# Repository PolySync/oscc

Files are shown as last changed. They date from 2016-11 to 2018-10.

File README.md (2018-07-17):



Open Source Car Control (OSCC) is an assemblage of software and hardware designs that enable computer control of modern cars in order to facilitate the development of autonomous vehicle technology. It is a modular and stable way of using software to interface with a vehicle’s communications network and control systems.

OSCC enables developers to send control commands to the vehicle, read control messages from the vehicle’s OBD-II CAN network, and forward reports for current vehicle control state. Such as steering angle & wheel speeds. Control commands are issued to the vehicle component ECUs via the steering wheel torque sensor, throttle position sensor, and brake position sensor. (Because the gas-powered Kia Soul isn’t brake by-wire capable, an auxiliary actuator is added to enable braking.) This low-level interface means that OSCC offers full-range control of the vehicle without altering the factory safety-case, spoofing CAN messages, or hacking ADAS features.

Although OSCC currently supports only the 2014 or later Kia Soul (petrol and EV), the API and firmware have been designed to make it easy to add new vehicle support. Additionally, the separation between API and firmware means it is easier to modify and test parts of your program without having to update the flashed OSCC modules.

Our [Wiki](https://github.com/PolySync/OSCC/wiki) is in the process of being updated to reflect the new changes, but contains a bunch of valuable information to help you get started in understanding the details of the system.

**DriveKit:** If you're looking for a turn-key solution, we offer a commercially-supported vehicle control interface called DriveKit. DriveKit is a complete system for by-wire control of Kia Soul EV and Kia Niro Hybrid vehicles. It includes an integrated control module, automotive-grade wiring harnesses, e-stop switch, and additional vehicle control features –– plus it installs in under an hour. **Visit https://polysync.io/drivekit/ for more information.**

# Versions

New versions of the API and the firmware are released periodically as new features are added and bugs are
fixed. **It is of vital importance that you update whenever there is a new version so that you can be certain
you are not using a version with known safety issues.**

There are four versions to be aware of:

* **Sensor Interface Board (throttle and steering):** the version is printed on the front of the shield

* **Vehicle Control Module (EV brakes):** the version is printed on the front of the shield

* **Actuator Control Board (petrol brakes):** the version is printed on the front of the shield

* **API and Firmware:** a single version is shared by both and listed in the [Releases section](https://github.com/PolySync/oscc/releases) of the repository.

The following table can be used to ensure that you use the appropriate firmware version with your boards:

| | Board Version | Firmware Version |
| --- | --- | --- |
| Sensor Interface | >= 1.0.0 | >= 1.0.0 |
| Vehicle Control | 0.1.0 | >= 1.1.0 |
| Actuator Control | >= 1.2.0 | >= 1.0.0 |
| | < 1.2.0 __*__ | >= 1.0.1 |

__*__ *Later versions of the Actuator Control Board utilize new pins to perform additional safety checks on startup. To use the new firmware on older boards, please see additional instructions in the [build](#brake-startup-test) section.*

# Repository Contents

* **api** - Software API, so your program can seamlessly talk to our modules.
* **firmware** - Arduino libraries and firmware for the OSCC modules.
* **hardware** - PCB schematics and board designs for control modules.

# Boards

The sensor interface and actuator control board schematics and design files are located in the
`hardware/boards` directory.

Thanks to [Trey German](https://www.polymorphiclabs.com) for
help designing the boards.

# Building and Uploading Firmware

The OSCC Project is built around a number of individual firmware modules that inter-operate to allow communication with your vehicle.
These modules are built from Arduinos and Arduino shields designed specifically for interfacing with various vehicle components.
Once these modules have been installed in the vehicle and flashed with the firmware, the API can be used to
receive reports from the car and send spoofed commands.

## Pre-requisites

You must have Arduino Core (version 1.8.5 or greater) and CMake (version 2.8 or greater) installed on
your machine.

```
sudo apt install build-essential cmake
```

A manual Arduino install is required since the debian package is older than 1.8.5
```
sudo apt-get purge arduino arduino-core
wget http://arduino.cc/download.php?f=/arduino-1.8.5-linux64.tar.xz -O arduino-1.8.5.tar.xz
tar -xf arduino-1.8.5.tar.xz
cd arduino-1.8.5
sudo mkdir -p /usr/share/arduino
sudo cp -R * /usr/share/arduino
```

OSCC uses CMake to avoid some of the limitations of the Arduino IDE. Using this method you can build
and upload the firmware from the command-line.

Check out [Arduino CMake](https://github.com/arduino-cmake/arduino-cmake) for more information.

## Building the Firmware

Navigate to the `firmware` directory and create a build directory inside of it:

```
cd firmware
mkdir build
cd build
```

To generate Makefiles, tell `cmake` which vehicle to build for by supplying the
appropriate build flag:

| Vehicle | Flag |
| --- | --- |
| Kia Soul Petrol | -DVEHICLE=kia_soul |
| Kia Soul EV | -DVEHICLE=kia_soul_ev |
| Kia Niro | -DVEHICLE=kia_niro |

For example, if you want to build firmware for the petrol Kia Soul:

```
cmake .. -DVEHICLE=kia_soul
```

**Operator Overrides: While all OSCC modules have operator override detection enabled by default, attempting to grab the steering wheel while the system is active could result in serious injury. The preferred method of operator override for steering is to utilize the brake pedal or E-stop button. To disable operator override for the steering module, pass an additional flag to the CMake build step.**

```
cmake .. -DVEHICLE=kia_soul -DSTEERING_OVERRIDE=OFF
```

If steering operator overrides remain enabled, the sensitivity can be adjusted by changing the value of the `TORQUE_DIFFERENCE_OVERRIDE_THRESHOLD` in the corresponding vehicle's header file.

* Lowering this value will make the steering module more sensitive to operator override, but will result in false positives around high-torque areas, such as the mechanical limits of the steering rack or when quickly and rapidly changing direction.
* Increasing this value will result in fewer false positives, but will make it more difficult to manually override the wheel.

By default, your firmware will have debug symbols which is good for debugging but increases
the size of the firmware significantly. To compile without debug symbols and optimizations
enabled, use the following instead:

```
cmake .. -DVEHICLE=kia_soul -DCMAKE_BUILD_TYPE=Release
```

**NOTE:**
> For older (< 1.2.0) versions of the actuator control board, you need to set an additional flag using `cmake .. -DKIA_SOUL=ON -DBRAKE_STARTUP_TEST=OFF` to disable startup tests that are not compatible with the previous board design.

This will generate the necessary files for building.

Now you can build all of the firmware with `make`:

```
make
```

If you'd like to build only a specific module, you can provide a target name to
`make` for whichever module you'd like to build:

```
make brake
make can-gateway
make steering
make throttle
```

## Uploading the Firmware

Once the firmware is successfully built, you can upload it. When you connect to
an Arduino with a USB cable, your machine assigns a serial device to it with the
path `/dev/ttyACM#` where `#` is a digit starting at 0 and increasing by one with
each additional Arduino connected.

You can upload firmware to a single module or to all modules. By default, `cmake`
is configured to expect each module to be `/dev/ttyACM0`, so if you connect a
single module to your machine, you can flash it without changing anything:

```
make throttle-upload
```

However, if you want to flash all modules, you need to change the ports in
`cmake` for each module to match what they are on your machine. The easiest way
is to connect each module in alphabetical order (brake, CAN gateway, steering,
throttle) so that they are assigned `/dev/ttyACM0` through `/dev/ttyACM3` in
a known order. You can then change the ports during the `cmake ..` step:

```
cmake .. -DVEHICLE=kia_soul -DSERIAL_PORT_BRAKE=/dev/ttyACM0 -DSERIAL_PORT_CAN_GATEWAY=/dev/ttyACM1 -DSERIAL_PORT_STEERING=/dev/ttyACM2 -DSERIAL_PORT_THROTTLE=/dev/ttyACM3
```

Then you can flash all with one command:

```
make all-upload
```

Sometimes it takes a little while for the Arduino to initialize once connected, so if there is an
error thrown initially, wait a little bit and then retry the command.

## Monitoring Arduino Modules

It is sometimes useful to monitor individual Arduino modules to check for proper operation and to
debug. If the modules have been built with the flag `-DCMAKE_BUILD_TYPE=Debug`, their debug
printing functionality will be enabled and they will print status information to the serial interface.

The GNU utility `screen` is one option to communicate with the Arduino via serial over USB. It can
be used to both receive the output of any `Serial.print` statements in your Arduino code, and to
push commands over serial to the Arduino. If you don't already have it installed,
you can get it with the following command:

```
sudo apt install screen
```

You need to enable debug mode with `-DDEBUG=ON` and tell `cmake` what serial port
the module you want to monitor is connected to
(see [section on uploading](#uploading-the-firmware) for details on the default
ports for each module). The default baud rate is `115200` but you can change it:

```
cmake .. -DVEHICLE=kia_soul -DDEBUG=ON -DSERIAL_PORT_THROTTLE=/dev/ttyACM0 -DSERIAL_BAUD_THROTTLE=19200
```

You can use a module's `monitor` target to automatically run `screen`, or a
module's `monitor-log` target to run `screen` and output to a file called
`screenlog.0` in the module's build directory:

```
make brake-monitor
make brake-monitor-log
```

You can exit `screen` with `C-a \`.

To do more in-depth debugging you can use any of a number of serial monitoring applications.
Processing can be used quite effectively to provide output plots of data incoming across a serial
connection.

Be aware that using serial printing can affect the timing of the firmware. You may experience
strange behavior while printing that does not occur otherwise.

# Controlling Your Vehicle - an Example Application

Now that all your Arduino modules are properly setup, it is time to start sending control commands.

We've created an example application, joystick commander, that uses the OSCC API to interface with the firmware, allowing you to send commands using a game controller and receive reports from the on-board OBD-II CAN. These commands are converted into CAN messages, which the OSCC API sends to the respective Arduino modules and are used to actuate the vehicle.

[OSCC Joystick Commander](https://github.com/PolySync/oscc-joystick-commander)

We've also created a ROS node, that uses the OSCC API to interface with the firmware from ROS messages, allowing you to send commands and receive reports in ROS.

[ROSCCO](https://github.com/PolySync/roscco)

# OSCC API

**Open and close CAN channel to OSCC Control CAN.**

```c
oscc_result_t oscc_open( uint channel );
oscc_result_t oscc_close( uint channel );
```

These methods are the start and end points of using the OSCC API in your application. ```oscc_open``` will open a socket connection
on the specified CAN channel, enabling it to quickly receive reports from and send commands to the firmware modules.
When you are ready to terminate your application, ```oscc_close``` can terminate the connection.

**NOTE:**
> The OSCC API catches the SIGIO signal which is asserted when a CAN frame is received on the CAN socket, and sets up a SIGIO signal handler
> to forward valid CAN messages to your application. If you have a section of code that is susceptible to conflicts with interrupts,
> you should temporarily block the SIGIO signal for the duration of that section and unblock it afterward.

**Enable and disable all OSCC modules.**

```c
oscc_result_t oscc_enable( void );
oscc_result_t oscc_disable( void );
```

After you have initialized your CAN connection to the firmware modules, these methods can be used to enable or disable the system. This
allows your application to choose when to enable sending commands to the firmware. Although you can only send commands when the system is
enabled, you can receive reports at any time.

**Publish control command to the corresponding module.**

```c
oscc_result_t publish_brake_position( double normalized_position );
oscc_result_t publish_steering_torque( double normalized_torque );
oscc_result_t publish_throttle_position( double normalized_position );
```

These commands will forward a double value to the specified firmware module. The double values are [0.0, 1.0] for brake and throttle,
and [-1.0, 1.0] for steering where -1.0 is counterclockwise and 1.0 is clockwise. The API will construct the appropriate values to send
as spoofed voltages to the vehicle to achieve the desired state. The API also contains safety checks to ensure no voltages outside of
the vehicle's expected range are sent.

**NOTE:**
> Each of these functions must be called at least once every 200ms to prevent the modules from detecting a loss of communication to the
> controlling computer (at which point they would disable themselves).

**Register callback function to handle OSCC report and OBD messages.**

```c
oscc_result_t subscribe_to_brake_reports( void(*callback)(oscc_brake_report_s *report) );
oscc_result_t subscribe_to_steering_reports( void(*callback)(oscc_steering_report_s *report) );
oscc_result_t subscribe_to_throttle_reports( void(*callback)(oscc_throttle_report_s *report) );
oscc_result_t subscribe_to_fault_reports( void(*callback)(oscc_fault_report_s *report) );
oscc_result_t subscribe_to_obd_messages( void(*callback)(struct can_frame *frame) );
```

In order to receive reports from the modules, your application will need to register a callback handler with the OSCC API.
When the appropriate report for your callback function is received from the API's socket connection, it will then forward the
report to your software.

Each module's reports are described in their respective wiki sections:

* [Brake (EV)](https://github.com/PolySync/oscc/wiki/Firmware-Brake-%28EV%29#brake-report)
* [Brake (Petrol)](https://github.com/PolySync/oscc/wiki/Firmware-Brake-%28Petrol%29#brake-report)
* [Steering](https://github.com/PolySync/oscc/wiki/Firmware-Steering#steering-report)
* [Throttle](https://github.com/PolySync/oscc/wiki/Firmware-Throttle#throttle-report)

In addition to OSCC specific reports, it will also forward any non-OSCC reports to any callback function registered with
```subscribe_to_obd_messages```. This can be used to view CAN frames received from the vehicle's OBD-II CAN channel. If you know
the corresponding CAN frame's id, you can parse reports sent from the car.

# Tests

There are two types of tests available: unit and property-based.

## Test Dependencies

The unit tests and property-based tests each have their own set of dependencies
required to run the tests.

For the unit tests you must have **Cucumber 2.0.0** and its dependency **Boost** installed:

```
sudo apt install ruby-dev libboost-dev
sudo gem install cucumber -v 2.0.0
```

For the property-based tests you must have **Rust**, its build manager **Cargo**, and **libclang**:

```
sudo apt install rustc cargo clang libclang-dev
```

## Running Tests

Building and running the tests is similar to the firmware itself, but you must instead tell
`cmake` to build the tests instead of the firmware with the `-DTESTS=ON` flag. We also pass
the `-DCMAKE_BUILD_TYPE=Release` flag so that `cmake` will disable debug symbols and enable
optimizations, good things to do when running tests to ensure nothing breaks with
optimizations. Lastly, you must tell the tests which vehicle header to use for
the tests (e.g., `-DVEHICLE=kia_soul`).

```
cd firmware
mkdir build
cd build
cmake .. -DTESTS=ON -DCMAKE_BUILD_TYPE=Release -DVEHICLE=kia_soul
```

### Unit Tests

Each module has a suite of unit tests that use **Cucumber** with **Cgreen**. There are pre-built
64-bit Linux versions in `firmware/common/testing/framework`.

Boost is required for Cucumber-CPP and has been statically linked into `libcucumber-cpp.a`.
If you need to build your own versions you can use the provided script `build_test_framework.sh`
which will install the Boost dependencies (needed for building), clone the needed
repositories with specific hashes, build the Cgreen and Cucumber-CPP libraries,
and place static Boost in the Cucumber-CPP library.

The built libraries will be placed in an `oscc_test_framework` directory in the
directory that you ran the script from. You can then copy `oscc_test_framework/cucumber-cpp`
and `oscc_test_framework/cgreen` to `firmware/common/testing/framework`.

We can run all of the unit tests available:

```
make run-unit-tests
```

Each module's test can also be run individually:

```
make run-brake-unit-tests
make run-can-gateway-unit-tests
make run-steering-unit-tests
make run-throttle-unit-tests
```

If everything works correctly you should see something like this:

```
# language: en
Feature: Receiving commands

  Commands received from a controller should be processed and acted upon.

  Scenario Outline: Enable throttle command sent from controller        # firmware/throttle/tests/features/receiving_commands.feature:8
    Given throttle control is disabled                                  # firmware/throttle/tests/features/receiving_commands.feature:9
    And the accelerator position sensors have a reading of <sensor_val> # firmware/throttle/tests/features/receiving_commands.feature:10
    When an enable throttle command is received                         # firmware/throttle/tests/features/receiving_commands.feature:12
    Then control should be enabled                                      # firmware/throttle/tests/features/receiving_commands.feature:14
    And the last command timestamp should be set                        # firmware/throttle/tests/features/receiving_commands.feature:15
    And <dac_a_val> should be written to DAC A                          # firmware/throttle/tests/features/receiving_commands.feature:16
    And <dac_b_val> should be written to DAC B                          # firmware/throttle/tests/features/receiving_commands.feature:17

    Examples:
      | sensor_val | dac_a_val | dac_b_val |
      | 0          | 0         | 0         |
      | 256        | 1024      | 1024      |
      | 512        | 2048      | 2048      |
      | 1024       | 4096      | 4096      |
```

### Property-Based Tests

The throttle, steering, and brake modules, along with the PID controller library, also contain a series of
property-based tests.

We can run all of the property-based tests available:

```
make run-property-tests
```

Each module's test can also be run individually:

```
make run-brake-property-tests
make run-steering-property-tests
make run-throttle-property-tests
make run-pid-library-property-tests
```

Once the tests have completed, the output should look similar to the following:

```
running 7 tests
test check_integral_term ... ok
test check_derivative_term ... ok
test check_proportional_term ... ok
test check_reversed_inputs ... ok
test check_same_control_for_same_inputs ... ok
test check_zeroize ... ok

test result: ok. 7 passed; 0 failed; 0 ignored; 0 measured

   Doc-tests tests

running 0 tests

test result: ok. 0 passed; 0 failed; 0 ignored; 0 measured
```

### All Tests

Finally, as a convenience you can run all available tests:

```
make run-all-tests
```

# Additional Vehicles & Contributing

OSCC currently has information regarding the Kia Soul PS (2014-2018), but we want to grow! The
repository is structured to facilitate including more vehicles as more is learned about them.

In order to include information related to a new vehicle's specification, follow the format defined in ```api/include/vehicles/kia_soul.h``` and
add a `cmake` option to choose your new header when compiling the API.

Please see [CONTRIBUTING.md](CONTRIBUTING.md).

# License Information

Hardware source materials (e.g. schematics, board layouts, wiring diagrams, data sheets, physical
installation documentation, 3D models, etc.) for the OSCC (Open Source Car Control) Project are
licensed under Creative Commons Attribution-ShareAlike 4.0 International (CC BY-SA 4.0).

Firmware  and software source for the OSCC (Open Source Car Control) Project is licensed under the
MIT License (MIT) unless otherwise noted (e.g. 3rd party dependencies, etc.).

Please see [LICENSE.md](LICENSE.md) for more details.

# Contact Information

Please direct questions regarding OSCC and/or licensing to help@polysync.io.

*Distributed as-is; no warranty is given.*

Copyright (c) 2017 PolySync Technologies, Inc.  All Rights Reserved.

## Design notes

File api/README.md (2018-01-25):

# Getting started with the OSCC API

There are a few options on how to get started with your own application that
uses the OSCC API.

## The library approach

To build both `libosccapi.so` and `libosccapi.a` for the Kia Soul EV,
you can run the following commands on Linux from this directory.
```
mkdir build && cd build
cmake -DKIA_SOUL_EV=ON ..
make
```
Substitute `-DKIA_SOUL_EV` for another supported vehicle if the EV isn't your
target. For example `-DKIA_SOUL=ON` will build the libraries with support
for the Kia Soul Petrol instead.

### Using `libosccapi.so`
Using the shared library for a project that uses the OSCC API is easy!
The following is an example `CMakeLists.txt` for doing just that. This example
is all you need for a project with it's own source file, `main.c`.
```
cmake_minimum_required(VERSION 2.8)
project(an_example)
set(OSCC_API_INSTALL /path_to/oscc_directory/api)
link_directories(${OSCC_API_INSTALL}/build)
set(OSCC_INCLUDES ${OSCC_API_INSTALL}/include)
set(SOURCES ${CMAKE_SOURCE_DIR}/src/main.c)
add_executable(${PROJECT_NAME} ${SOURCES})
target_include_directories(${PROJECT_NAME} PUBLIC ${OSCC_INCLUDES})
target_link_libraries(${PROJECT_NAME} PUBLIC osccapi)
```

### Using `libosccapi.a`
Using the static library isn't much different than the shared one,
the CMakeLists.txt just requires the full path to the library as it doesn't
intuit it from a provided link_directory.
```
cmake_minimum_required(VERSION 2.8)
project(an_example)
set(OSCC_API_INSTALL /path_to/oscc_directory/api)
set(OSCC_INCLUDES ${OSCC_API_INSTALL}/include)
set(SOURCES ${CMAKE_SOURCE_DIR}/src/main.c)
add_executable(${PROJECT_NAME} ${SOURCES})
target_include_directories(${PROJECT_NAME} PUBLIC ${OSCC_INCLUDES})
target_link_libraries(${PROJECT_NAME} PUBLIC ${OSCC_API_INSTALL}/build/libosccapi.a)
```

## Straight from the sources
Another approach is to just include the OSCC API source code in your project.
Since the OSCC API has no dependencies beyond a Linux system, this is easy too!
Here's an example CMakeLists.txt that takes the straight from the sources
approach. Note that it makes the assumption that we're building for the Kia
Soul Petrol with the `"-DKIA_SOUL=ON"`.

```
cmake_minimum_required(VERSION 2.8)
project(an_example)
set(OSCC_API_INSTALL /path_to/oscc_directory/api)
set(OSCC_INCLUDES ${OSCC_API_INSTALL}/include ${OSCC_API_INSTALL}/src)
set(SOURCES ${CMAKE_SOURCE_DIR}/src/main.c ${OSCC_API_INSTALL}/src/oscc.c)
add_executable(${PROJECT_NAME} ${SOURCES})
target_compile_definitions(${PROJECT_NAME} PUBLIC "-DKIA_SOUL=ON")
target_include_directories(${PROJECT_NAME} PUBLIC ${OSCC_INCLUDES})
```

## Using the API

Let's walk through actually writing some code that uses the OSCC API, an example
program that listens to all the information that OSCC reports. Feel free to
experiment with this code, if it's all put into a `main.c` you can use
any of the CMakeLists.txt options above to build it.

First, we'll do some generic setup. This isn't a requriement of the OSCC API
but might make our example a little more useful.

```
#include <stdio.h> // printf
#include <signal.h> // SIGINT
#include <unistd.h> // usleep
```
Okay, now for the actual OSCC API include that allows us to initiate,
listen to each message type and then properly release OSCC. `oscc.h` is
all you need!

```
#include "oscc.h" // oscc_open, oscc_disable, oscc_close and each subscribe.
```
In order for our example to trigger the proper cleanup when we press `Ctrl+C`
to quit the program, we'll setup a signal handler to let us know.

```
// Global indication of Ctrl+C.
static int EXIT_SIGNALED = OSCC_OK;

// Help exiting gracefully.
void signal_handler(int signal_number)
{
    if (signal_number == SIGINT)
    {
        EXIT_SIGNALED = OSCC_ERROR;
    }
}
```

Now lets walk through our OSCC message subscribers. When we get a report from
something OSCC provides, let's print a message reporting what we see.

__Throttle__
```
void throttle_callback(oscc_throttle_report_s * report)
{
    printf("Hello from throttle_callback!\n");
}
```
__Steering__
```
void steering_callback(oscc_steering_report_s * report)
{
    printf("steering_callback reporting!\n");
}
```
__Brake__
```
void brake_callback(oscc_brake_report_s * report)
{
    printf("'Brake-ing' news from the brake_callback!\n");
}
```
__Fault__
```
void fault_callback(oscc_fault_report_s * report)
{
    printf("Oh! Something caused a fault and we made it to the fault_callback. We're seeing a ");

    if (report->fault_origin_id == FAULT_ORIGIN_BRAKE)
    {
        printf("brake fault!\n");
    }
    else if (report->fault_origin_id == FAULT_ORIGIN_STEERING)
    {
        printf("steering fault!\n");
    }
    else if (report->fault_origin_id == FAULT_ORIGIN_THROTTLE)
    {
        printf("throttle fault!\n");
    }
}
```
__OBD__
```
static void obd_callback(struct can_frame * frame)
{
    printf("From the obd_callback, CAN ID: %x\n", frame->can_id);
}
```
Okay, we're all setup! Let get to work! Our code base is pretty small so
we'll just stick to the `main` function
```
int main
{
```
Now let's put that 'Ctrl+C' setup we did earlier to use.
```
    struct sigaction sig;
    sig.sa_handler = signal_handler;
    sigaction(SIGINT, &sig, NULL);
```
Next we need to tell OSCC where to to send it's messages.
```
    oscc_subscribe_to_obd_messages(obd_callback);
    oscc_subscribe_to_brake_reports(brake_callback);
    oscc_subscribe_to_steering_reports(steering_callback);
    oscc_subscribe_to_throttle_reports(throttle_callback);
    oscc_subscribe_to_fault_reports(fault_callback);
```
In order to verify that initalizing OSCC succeeds and clean things up
if we fail, we need a way to capture results.
```
    oscc_result_t return_value;
```
For brevity, we'll assume that we're opening CAN channel 0 to connect to OSCC
and spin it up!
```
    int channel = 0;
    return_value = oscc_open(channel);
```
Since we captured the result of out call to oscc_open, we can verify it
succeded before moving on or signal that we need to clean things up.
```
    if(return_value != OSCC_OK)
    {
        printf("Error in oscc_open!\n");
        EXIT_SIGNALED = OSCC_ERROR;
    }
```

Now we wait, just let the callbacks to their work. To avoid loading the
CPU with this example, we'll sleep for a bit (50ms) on each iteration.
```
    while(EXIT_SIGNALED == OSCC_OK)
    {
        (void) usleep(50000);
    }
```

Once we're through, we can clean things up.
```
    oscc_disable();
    oscc_close(channel);
```

Don't forget to close up the `main` function!
```
}
```

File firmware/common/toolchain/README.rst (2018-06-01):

=============
Arduino CMake
=============


Arduino is a great development platform, which is easy to use. It has everything a beginner should need. The *Arduino IDE* simplifies a lot of things for the standard user, but if you are a professional programmer the IDE can feel simplistic and restrictive.

One major drawback of the *Arduino IDE* is that you cannot do anything without it, which for me is a **complete buzz kill**. Thats why queezythegreat created an alternative build system for the Arduino using CMake. With the original repository not being updated since 2014 and lacking some important features like support for the latest Arduino SDKs, we decided to fix things up for 1.6; now that some people have started using this as their preferred fork, we decided to accept our fate of being the current maintainers.

CMake is great cross-platform build system that works on practically any operating system. With it you are not constrained to a single build system. CMake lets you generate the build system that fits your needs, using the tools you like. It can generate any type of build system, from simple Makefiles, to complete projects for Eclipse, Visual Studio, XCode, etc.

The **Arduino CMake** build system integrates tightly with the *Arduino SDK*.

*Arduino SDK* version **0.19** or higher is required.

So if you like to do things from the command line (using make), or to build your firmware where you're in control, or if you would like to use an IDE such as Eclipse, KDevelop, XCode, CodeBlocks or something similar,  then **Arduino CMake** is the system for you.

Features
--------

* Integrates with *Arduino SDK*
* Supports all Arduino boards.
* Supports Arduino type libraries.
* Automatic detection of Arduino libraries.
* Generates firmware images.
* Generates built-in examples.
* Generates libraries.
* Sketch support.
* Upload support.
* Hardware Platform support.
* Programmer support (with bootloader upload).
* Supports multiple build system types (Makefiles, Eclipse, KDevelop, CodeBlocks, XCode, etc).
* Cross-platform: Windows, Linux, Mac.
* Extensible build system, thanks to CMake.

Feedback
--------

**Arduino CMake** is hosted on GitHub and is available on multiple forks (At the time of writing up to **161(!)**),
with one the more advanced and maintainable being the following:

https://github.com/arduino-cmake/arduino-cmake/

However, none of this would have been possible with the generous bunch of work the original author queezythegreat invested into this project, who definately earns most of the credit for getting things running:

https://github.com/queezythegreat/arduino-cmake

We want to stress again that he did all the initial work to even make CMake spit out Arduino firmwares. Without the effort queezythegreat put into this, we would not have been able to even think about getting an Arduino 1.6 project running. This is by no means a hostile fork and we would give him ownership of the organization as well at any time, should he wish so.

Did you find a bug or would like a specific feature, please report it at:

https://github.com/arduino-cmake/arduino-cmake/issues

If you would like to hack on this project, don't hesitate to fork it on GitHub.
We will be glad to integrate your changes if you send me a ``Pull Request``.

Requirements
------------

* Base requirements:

  - ``CMake`` - http://www.cmake.org/cmake/resources/software.html
  - ``Arduino SDK`` - http://www.arduino.cc/en/Main/Software

* Linux requirements:

  - ``gcc-avr``      - AVR GNU GCC compiler
  - ``binutils-avr`` - AVR binary tools
  - ``avr-libc``     - AVR C library
  - ``avrdude``      - Firmware uploader

Contributors
------------

I would like to thank the following people for contributing to **Arduino CMake**:

* Juan José Herrero Barbosa (`Souler`_)
* Bei Chen Liu (`Baycken`_)
* MrPointer (`MrPointer`_)
* Marc Plano-Lesay (`Kernald`_)
* James Goppert (`jgoppert`_)
* Matt Tyler (`matt-tyler`_)
* Andrew Stromme (`astromme`_)
* `johnyb`_
* `arunh`_
* Sebastian Herp (`sebastianherp`_)
* Michael Daffin (`james147`_)
* Pavel Ilin (`PIlin`_)
* Igor Mikolic-Torreira (`igormiktor`_)
* Claudio Henrique Fortes Felix (`chffelix`_)
* Alexandre Tuleu (`atuleu`_)
* `getSurreal`_
* Sebastian Zaffarano (`szaffarano`_)
* `cheshirekow`_
* Logan Engstrom (`meadowstream`_) 
* Francisco Ramírez (`franramirez688`_)
* Brendan Shillingford (`bshillingford`_)
* Mike Purvis (`mikepurvis`_) 
* Steffen Hanikel (`hanikesn`_)
* Tomasz Bogdal (`queezythegreat`_) (original author of arduino-cmake)
* Jonas (`JonasProgrammer`_)

.. _Souler: https://github.com/Souler
.. _Baycken: https://github.com/Baycken
.. _MrPointer: https://github.com/MrPointer
.. _Kernald: https://github.com/Kernald
.. _jgoppert: https://github.com/jgoppert
.. _matt-tyler: https://github.com/matt-tyler
.. _astromme: https://github.com/astromme
.. _johnyb: https://github.com/johnyb
.. _arunh: https://github.com/arunh
.. _sebastianherp: https://github.com/sebastianherp
.. _james147: https://github.com/james147
.. _PIlin: https://github.com/PIlin
.. _igormiktor: https://github.com/igormiktor
.. _chffelix: https://github.com/chffelix
.. _atuleu: https://github.com/atuleu
.. _getSurreal: https://github.com/getSurreal
.. _szaffarano: https://github.com/szaffarano
.. _cheshirekow: https://github.com/cheshirekow
.. _meadowstream: https://github.com/meadowstream
.. _franramirez688: https://github.com/franramirez688
.. _bshillingford: https://github.com/bshillingford
.. _mikepurvis: https://github.com/mikepurvis
.. _hanikesn: https://github.com/hanikesn
.. _queezythegreat: https://github.com/queezythegreat
.. _JonasProgrammer: https://github.com/JonasProgrammer

License
-------
This Source Code Form is subject to the terms of the Mozilla Public
License, v. 2.0. If a copy of the MPL was not distributed with this file,
You can obtain one at http://mozilla.org/MPL/2.0/.

TODO
----

* Test more complex configurations and error handling

Contents
--------

1. `Getting Started`_
2. `Using Arduino CMake`_

   1. `Creating Firmware Images`_
   2. `Creating Libraries`_
   3. `Arduino Sketches`_
   4. `Arduino Built-in Examples`_
   5. `Arduino Libraries`_
   6. `Arduino Library Examples`_
   7. `Compiler and Linker Flags`_
   8. `Programmers`_
   9. `Pure AVR Development`_
   10. `Advanced Options`_
   11. `Miscellaneous Functions`_
   12. `Bundling Arduino CMake`_

3. `Linux Environment`_

   1. `Linux Serial Naming`_
   2. `Linux Serial Terminals`_

4. `Mac OS X Environment`_

   1. `Mac Serial Naming`_
   2. `Mac Serial Terminals`_

5. `Windows Environment`_

   1. `CMake Generators`_
   2. `Windows Serial Naming`_
   3. `Windows Serial Terminals`_

6. `Eclipse Environment`_
7. `Troubleshooting`_

   1. `undefined reference to `__cxa_pure_virtual'`_
   2. `Arduino Mega 2560 image does not work`_
   3. `Library not detected automatically`_
   4. `error: attempt to use poisoned "SIG_USART0_RECV"`_

8. `Resources`_

Getting Started
---------------

The following instructions are for **\*nix** type systems, specifically this is a Linux example.

In short you can get up and running using the following commands::

    mkdir build
    cd build
    cmake ..
    make
    make upload              # to upload all firmware images             [optional]
    make blink-serial  # to get a serial terminal to wire_serial   [optional]

For a more detailed explanation, please read on...

1. Toolchain file
   
   In order to build firmware for the Arduino you have to specify a toolchain file to enable cross-compilation. There are two ways of specifying the file, either at the command line or from within the *CMakeLists.txt* configuration files. The bundled example uses the second approach like so::

        set(CMAKE_TOOLCHAIN_FILE ${CMAKE_SOURCE_DIR}/cmake/ArduinoToolchain.cmake)

   Please note that this must be before the ``project(...)`` command.
   
   If you would like to specify it from the command line, heres how::

        cmake -DCMAKE_TOOLCHAIN_FILE=../path/to/toolchain/file.cmake PATH_TO_SOURCE_DIR

2. Creating a build directory

   The second order of business is creating a build directory. CMake has a great feature called out-of-source builds, what this means is the building is done in a completely separate directory from where the sources are. The benefit of this is you don't have any clutter in you source directory and you won't accidentally commit something that is auto-generated.

   So let's create that build directory::

        mkdir build
        cd build

3. Creating the build system

   Now let's create the build system that will create our firmware::

        cmake ..

   To specify the build system type, use the ``-G`` option, for example::

        cmake -G"Eclipse CDT4 - Unix Makefiles" ..

   If you rather use a GUI, use::

        cmake-gui ..

4. Building

   Next we will build everything::

        make

5. Uploading

   Once everything built correctly we can upload. Depending on your Arduino you will have to update the serial port used for uploading the firmware. To change the port please edit the following variable in *CMakeLists.txt*::

        set(${FIRMWARE_NAME}_PORT /path/to/device)

   Ok lets do a upload of all firmware images::

        make upload

   If you have an upload sync error then try resetting/ power cycling the board before starting the upload process.

6. Serial output

   If you have some serial output, you can launch a serial terminal from the build system. The command used for executing the serial terminal is user configurable by the following setting::

        set(${FIRMWARE_NAME}_SERIAL serial command goes here)

   In order to get access to the serial port use the following in your command::

        @SERIAL_PORT@

   That constant will get replaced with the actual serial port used (see uploading). In the case of our example configuration we can get the serial terminal by executing the following::

        make blink-serial

Using Arduino CMake
-------------------

In order to use **Arduino CMake** just include the toolchain file, everything will get set up for building. You can set the toolchain
in `CMakeList.txt` like so::

        set(CMAKE_TOOLCHAIN_FILE ${CMAKE_SOURCE_DIR}/cmake/ArduinoToolchain.cmake)

Please note that this must be before the ``project(...)`` command.

You can also specify it at build configuration time::

        cmake -DCMAKE_TOOLCHAIN_FILE=../path/to/toolchain/file.cmake PATH_TO_SOURCE_DIR

Creating Firmware Images
~~~~~~~~~~~~~~~~~~~~~~~~

Once you have the **Arduino CMake** loaded you can start defining firmware images.

To create Arduino firmware in CMake you use the ``generate_arduino_firmware`` command. The full syntax of the command is::

    generate_arduino_firmware(target_name
         [BOARD board_name]
         [BOARD_CPU board_cpu]
         [SKETCH sketch_path | SRCS  src1 src2 ... srcN]
         [HDRS  hdr1 hdr2 ... hdrN]
         [LIBS  lib1 lib2 ... libN]
         [PORT  port]
         [SERIAL serial_cmd]
         [PROGRAMMER programmer_id]
         [AFLAGS flags]
         [NO_AUTOLIBS])

The options are:

+--------------------+----------------------------------------------------------------------+----------------------------------------+
| **Name**           | **Description**                                                      | **REQUIRED**                           |
+--------------------+----------------------------------------------------------------------+----------------------------------------+
| **BOARD**          | Board name *(such as uno, mega2560, ...)*                            | **REQUIRED**                           |
+--------------------+----------------------------------------------------------------------+----------------------------------------+
| **BOARD_CPU**      | Board CPU *(such as atmega328, atmega168, ...)*                      | **REQUIRED** if board cpu is ambiguous |
+--------------------+----------------------------------------------------------------------+----------------------------------------+
| **SKETCH**         | Sketch path (see `Arduino Sketches`_)                                | **SKETCH or SRCS are REQUIRED**        |
+--------------------+----------------------------------------------------------------------+----------------------------------------+
| **SRCS**           | Source files                                                         | **SKETCH or SRCS are REQUIRED**        |
+--------------------+----------------------------------------------------------------------+----------------------------------------+
| **HDRS**           | Headers files *(for project based build systems)*                    |                                        |
+--------------------+----------------------------------------------------------------------+----------------------------------------+
| **LIBS**           | Libraries to link (see `Creating libraries`_)                        |                                        |
+--------------------+----------------------------------------------------------------------+----------------------------------------+
| **PORT**           | Serial port, for upload and serial targets (see `Upload Firmware`_)  |                                        |
+--------------------+----------------------------------------------------------------------+----------------------------------------+
| **SERIAL**         | Serial command for serial target (see `Serial Terminal`_)            |                                        |
+--------------------+----------------------------------------------------------------------+----------------------------------------+
| **PROGRAMMER**     | Programmer ID, enables programmer burning (see `Programmers`_).      |                                        |
+--------------------+----------------------------------------------------------------------+----------------------------------------+
| **ARDLIBS**        | Manual list of Arduino type libraries, common use case is when the   |                                        |
|                    | library header name does not match the librarie's directory name.    |                                        |
|                    | **ADVANCED OPTION!** Can be used in conjuction with **NO_AUTOLIBS**. |                                        |
+--------------------+----------------------------------------------------------------------+----------------------------------------+
| **AFLAGS**         | avrdude flags for target                                             |                                        |
+--------------------+----------------------------------------------------------------------+----------------------------------------+
| **NO_AUTOLIBS**    | Disable Arduino library detection *(default On)*                     |                                        |
+--------------------+----------------------------------------------------------------------+----------------------------------------+
| **MANUAL**         | Disable Arduino Core (enables pure AVR development)                  |                                        |
+--------------------+----------------------------------------------------------------------+----------------------------------------+

You can specify the options in two ways, either as the command arguments or as variables. When specifying the options as variables they must be named::

    ${TARGET_NAME}_${OPTION_NAME}

Where **${TARGET_NAME}** is the name of you target and **${OPTION_NAME}** is the name of the option.

So to create a target (firmware image) called ``blink``, composed of ``blink.h`` and ``blink.cpp`` source files for the *Arduino Uno*, you write the following::

    set(blink_SRCS  blink.cpp)
    set(blink_HDRS  blink.h)
    set(blink_BOARD uno)

    generate_arduino_firmware(blink)

The previous example can be rewritten as::

    generate_arduino_firmware(blink
          SRCS  blink.cpp
          HDRS  blink.h
          BOARD uno)

Upload Firmware
_______________

To enable firmware upload functionality, you need to add the ``PORT`` option::

    set(blink_SRCS  blink.cpp)
    set(blink_HDRS  blink.h)
    set(blink_PORT /dev/ttyUSB0)
    set(blink_BOARD nano)
    set(blink_BOARD_CPU atmega328) # required because nano has atmega328 and atmega168 models

    generate_arduino_firmware(blink)

Or::

    generate_arduino_firmware(blink
          SRCS  blink.cpp
          HDRS  blink.h
          PORT  /dev/ttyUSB0
          BOARD_CPU atmega328
          BOARD nano)

Once defined there will be two targets available for uploading, ``${TARGET_NAME}-upload`` and a global ``upload`` target (which will depend on all other upload targets defined in the build):

* ``blink-upload`` - will upload just the ``blink`` firmware
* ``upload`` - upload all firmware images registered for uploading

Serial Terminal
_______________
To enable serial terminal, use the ``SERIAL`` option (``@SERIAL_PORT@`` will be replaced with the ``PORT`` option)::

    set(blink_SRCS  blink.cpp)
    set(blink_HDRS  blink.h)
    set(blink_PORT  /dev/ttyUSB0)
    set(blink_SERIAL picocom @SERIAL_PORT@ -b 9600 -l)
    set(blink_BOARD uno)

    generate_arduino_firmware(blink)

Alternatively::

    generate_arduino_firmware(blink
          SRCS  blink.cpp
          HDRS  blink.h
          PORT  /dev/ttyUSB0
          SERIAL picocom @SERIAL_PORT@ -b 9600 -l
          BOARD uno)

This will create a target named ``${TARGET_NAME}-serial`` (in this example: blink-serial).

Creating Libraries
~~~~~~~~~~~~~~~~~~

Creating libraries is very similar to defining a firmware image, except we use the ``generate_arduino_library`` command. This command creates static libraries, and are not to be confused with `Arduino Libraries`_. The full command syntax::

    generate_arduino_library(name
         [BOARD board_name]
         [BOARD_CPU board_cpu]
         [SRCS  src1 src2 ... srcN]
         [HDRS  hdr1 hdr2 ... hdrN]
         [LIBS  lib1 lib2 ... libN]
         [NO_AUTOLIBS])

The options are:

+--------------------+------------------------------------------------------+----------------------------------------+
| **Name**           | **Description**                                      | **REQUIRED**                           |
+--------------------+------------------------------------------------------+----------------------------------------+
| **BOARD**          | Board name *(such as uno, mega2560, ...)*            | **REQUIRED**                           |
+--------------------+------------------------------------------------------+----------------------------------------+
| **BOARD_CPU**      | Board CPU *(such as atmega328, atmega168, ...)*      | **REQUIRED** if board cpu is ambiguous |
+--------------------+------------------------------------------------------+----------------------------------------+
| **SRCS**           | Source files                                         | **REQUIRED**                           |
+--------------------+------------------------------------------------------+----------------------------------------+
| **HDRS**           | Headers files *(for project based build systems)*    |                                        |
+--------------------+------------------------------------------------------+----------------------------------------+
| **LIBS**           | Libraries to link *(sets up dependency tracking)*    |                                        |
+--------------------+------------------------------------------------------+----------------------------------------+
| **NO_AUTOLIBS**    | Disable Arduino library detection *(default On)*     |                                        |
+--------------------+------------------------------------------------------+----------------------------------------+
| **MANUAL**         | Disable Arduino Core (enables pure AVR development)  |                                        |
+--------------------+------------------------------------------------------+----------------------------------------+

You can specify the options in two ways, either as the command arguments or as variables. When specifying the options as variables they must be named::

    ${TARGET_NAME}_${OPTION_NAME}

Where **${TARGET_NAME}** is the name of you target and **${OPTION_NAME}** is the name of the option.

Let's define a simple library called ``blink_lib`` with two sources files for the *Arduino Uno*::

    set(blink_lib_SRCS  blink_lib.cpp)
    set(blink_lib_HDRS  blink_lib.h)
    set(blink_lib_BOARD uno)

    generate_arduino_library(blink_lib)

The other way of defining the same thing is::

    generate_arduino_library(blink_lib
        SRCS  blink_lib.cpp
        HDRS  blink_lib.h
        BOARD uno)

Once that library is defined we can use it in our other firmware images... Let's add ``blink_lib`` to the ``blink`` firmware::

    set(blink_SRCS  blink.cpp)
    set(blink_HDRS  blink.h)
    set(blink_LIBS  blink_lib)
    set(blink_BOARD uno)

    generate_arduino_firmware(blink)

CMake has automatic dependency tracking, so when you build the ``blink`` target, ``blink_lib`` will automatically get built, in the right order.

Arduino Sketches
~~~~~~~~~~~~~~~~

To build a Arduino sketch use the **SKETCH** option (see `Creating firmware images`_). For example::

    set(blink_SKETCH  ${ARDUINO_SDK_PATH}/examples/1.Basics/Blink) # Path to sketch directory
    set(blink_BOARD   uno)

    generate_arduino_firmware(blink)

This will build the **blink** example from the **Arduino SDK**.

Note: When specifying the sketch directory path, arduino-cmake is expecting to find a sketch file named after the directory (with a extension of .pde or .ino).

You can also specify the path to the main sketch file, then the parent directory of that sketch will be search for additional sketch files.

Arduino Built-in Examples
~~~~~~~~~~~~~~~~~~~~~~~~~

The Arduino SDK comes with a handful of code examples, providing an easy setup for simple operations.
Since there are many examples, they were categorized, making each example be under a certain category.
Each example consists of at least one source file, named after the example and has the *.ino* or *.pde* extension, and sits under a directory which is also named after the example.
Each category is a directory named after it, having all its examples as sub-directories, named after them.
One such example is ``Blink``, probrably the most popular one as well. It's located under the ``Basics`` category and has a source file named ``Blink.ino``.

**Arduino CMake** has the abillity to automatically generate these examples, simply by passing their name and optionally their category, as some sort of an optimization. **It supports case-insensitive names**
If you would like to generate and upload some of those examples you can use the `generate_arduino_example` command. The syntax of the command is::

    generate_arduino_example(target_name
                             [EXAMPLE example_name]
                             [BOARD board_name]
                             [BOARD_CPU board_cpu]
                             [CATEGORY category_name]
                             [PORT port]
                             [SERIAL serial command]
                             [PORGRAMMER programmer_id]
                             [AFLAGS avrdude_flags])

The options are:

+--------------------+----------------------------------------------------------------------+----------------------------------------+
| **Name**           | **Description**                                                      | **REQUIRED**                           |
+--------------------+----------------------------------------------------------------------+----------------------------------------+
| **EXAMPLE**        | Example name.                                                        | **REQUIRED**                           |
+--------------------+----------------------------------------------------------------------+----------------------------------------+
| **BOARD**          | Board name *(such as uno, mega2560, ...)*                            | **REQUIRED**                           |
+--------------------+----------------------------------------------------------------------+----------------------------------------+
| **BOARD_CPU**      | Board CPU *(such as atmega328, atmega168, ...)*                      | **REQUIRED** if board cpu is ambiguous |
+--------------------+----------------------------------------------------------------------+----------------------------------------+
| **CATEGORY**       | Category name.                                                       |                                        |
+--------------------+----------------------------------------------------------------------+----------------------------------------+
| **PORT**           | Serial port, for upload and serial targets (see `Upload Firmware`_)  |                                        |
+--------------------+----------------------------------------------------------------------+----------------------------------------+
| **SERIAL**         | Serial command for serial target (see `Serial Terminal`_)            |                                        |
+--------------------+----------------------------------------------------------------------+----------------------------------------+
| **PROGRAMMER**     | Programmer ID, enables programmer burning (see `Programmers`_).      |                                        |
+--------------------+----------------------------------------------------------------------+----------------------------------------+
| **AFLAGS**         | avrdude flags for target                                             |                                        |
+--------------------+----------------------------------------------------------------------+----------------------------------------+

To generate a target for the **blink** example from the **Basics** category for the **Uno** board::

    generate_arduino_example(blink_example
                             CATEGORY Basics
                             EXAMPLE Blink
                             BOARD uno
                             PORT  /dev/ttyUSB0)

You can also rewrite the previous like so::

    set(blink_example_CATEGORY Basics)
    set(blink_example_EXAMPLE Blink)
    set(blink_example_BOARD uno)
    set(blink_example_PORT /dev/ttyUSB0)

    generate_arduino_example(blink_example)

The previous example will generate the following two target::

    blink_example
    blink_example-upload
    
**Note:** The above example will work perfectly fine even if the ``Basics`` category hadn't been passed.

Arduino Libraries
~~~~~~~~~~~~~~~~~

Libraries are one of the more powerful features which the Arduino offers to users. Instead of rewriting code, people bundle their code in libraries and share them with others.
The structure of these libraries is very simple, which makes them easy to create.

An Arduino library is **any directory which contains a header named after the directory**, simple.
Any source files contained within that directory are part of the library. Here is a example of library a called ExampleLib::

    ExampleLib/
      |-- ExampleLib.h
      |-- ExampleLib.cpp
      `-- OtherLibSource.cpp

Now because the power of Arduino lies within those user-created libraries, support for them is built right into **Arduino CMake**. The **Arduino SDK** comes with a large number of default libraries and adding new libraries is simple.

To incorporate a library into your firmware, you can do one of three things:

1. Place the library next to the default Arduino libraries (located at **${ARDUINO_SDK}/libraries**)
2. Place the library next to the firmware configuration file (same directory as the **CMakeLists.txt**)
3. Place the library in a separate folder and tell **Arduino CMake** the path to that directory.
   
   To tell CMake where to search for libraries use the `link_directories` command. The command has to be used before defining any firmware or libraries requiring those libraries.
   
   For example::
     
      link_directories(${CMAKE_CURRENT_SOURCE_DIR}/libraries)
      link_directories(/home/username/arduino_libraries)

If a library contains nested sources, a special option must be defined to enable recursion. For example to enable recursion for the Arduino Wire library use::

    set(Wire_RECURSE True)

The option name should be **${LIBRARY_NAME}_RECURSE**, where in this case **LIBRARY_NAME** is equal to *Wire*.

Arduino Libraries are not to be confused with normal static libraries (for exmaple *system libraries* or libraries created using generate_arduino_library). The **LIBS** option only accepts static libraries, so do not list the Arduino Libraries in that option (as you will get an error).

Arduino Library Examples
~~~~~~~~~~~~~~~~~~~~~~~~

Most Arduino libraries have examples bundled with them. If you would like to generate and upload some of those examples you can use the `generate_arduino_library_example` command. The syntax of the command is::

    generate_arduino_library_example(target_name
                             [LIBRARY library_name]
                             [EXAMPLE example_name]
                             [BOARD  board_name]
                             [BOARD_CPU board_cpu]
                             [PORT port]
                             [SERIAL serial command]
                             [PORGRAMMER programmer_id]
                             [AFLAGS avrdude_flags])

The options are:

+--------------------+----------------------------------------------------------------------+----------------------------------------+
| **Name**           | **Description**                                                      | **REQUIRED**                           |
+--------------------+----------------------------------------------------------------------+----------------------------------------+
| **LIBRARY**        | Library name.                                                        | **REQUIRED**                           |
+--------------------+----------------------------------------------------------------------+----------------------------------------+
| **EXAMPLE**        | Example name.                                                        | **REQUIRED**                           |
+--------------------+----------------------------------------------------------------------+----------------------------------------+
| **BOARD**          | Board name *(such as uno, mega2560, ...)*                            | **REQUIRED**                           |
+--------------------+----------------------------------------------------------------------+----------------------------------------+
| **BOARD_CPU**      | Board CPU *(such as atmega328, atmega168, ...)*                      | **REQUIRED** if board cpu is ambiguous |
+--------------------+----------------------------------------------------------------------+----------------------------------------+
| **PORT**           | Serial port, for upload and serial targets (see `Upload Firmware`_)  |                                        |
+--------------------+----------------------------------------------------------------------+----------------------------------------+
| **SERIAL**         | Serial command for serial target (see `Serial Terminal`_)            |                                        |
+--------------------+----------------------------------------------------------------------+----------------------------------------+
| **PROGRAMMER**     | Programmer ID, enables programmer burning (see `Programmers`_).      |                                        |
+--------------------+----------------------------------------------------------------------+----------------------------------------+
| **AFLAGS**         | avrdude flags for target                                             |                                        |
+--------------------+----------------------------------------------------------------------+----------------------------------------+

To generate a target for the **master_writer** example from the **Wire** library for the **Uno**::

    generate_arduino_library_example(wire_example
                             LIBRARY Wire
                             EXAMPLE master_writer
                             BOARD uno
                             PORT  /dev/ttyUSB0)

You can also rewrite the previous like so::

    set(wire_example_LIBRARY Wire)
    set(wire_example_EXAMPLE master_writer)
    set(wire_example_BOARD uno)
    set(wire_example_PORT /dev/ttyUSB0)

    generate_arduino_library_example(wire_example)

The previous example will generate the following two target::

    wire_example
    wire_example-upload

Compiler and Linker Flags
~~~~~~~~~~~~~~~~~~~~~~~~~

The default compiler and linker flags should be fine for most projects. If you required specific compiler/linker flags, use the following options to change them:

+--------------------------+----------------------+
|  **Name**                | **Description**      |
+--------------------------+----------------------+
| **ARDUINO_C_FLAGS**      | C compiler flags     |
+--------------------------+----------------------+
| **ARDUINO_CXX_FLAGS**    | C++ compiler flags   |
+--------------------------+----------------------+
| **ARDUINO_LINKER_FLAGS** | Linker flags         |
+--------------------------+----------------------+

Set these option either before the `project()` like so::

    set(ARDUINO_C_FLAGS      "-ffunction-sections -fdata-sections")
    set(ARDUINO_CXX_FLAGS    "${ARDUINO_C_FLAGS} -fno-exceptions")
    set(ARDUINO_LINKER_FLAGS "-Wl,--gc-sections")
    
    project(ArduinoExample C CXX)

or when configuring the project::

    cmake -D"ARDUINO_C_FLAGS=-ffunction-sections -fdata-sections" ../path/to/sources/

Programmers
~~~~~~~~~~~

**Arduino CMake** fully supports programmers for burning firmware and bootloader images directly onto the Arduino. 
If you have a programmer that is supported by the *Arduino SDK*, everything should work out of the box.
As of version 1.0 of the *Arduino SDK*, the following programmers are supported:

+--------------------+---------------------+
| **Programmer ID**  | **Description**     |
+--------------------+---------------------+
| **avrisp**         | AVR ISP             |
+--------------------+---------------------+
| **avrispmkii**     | AVRISP mkII         |
+--------------------+---------------------+
| **usbtinyisp**     | USBtinyISP          |
+--------------------+---------------------+
| **parallel**       | Parallel Programmer |
+--------------------+---------------------+
| **arduinoisp**     | Arduino as ISP      |
+--------------------+---------------------+

The programmers.txt file located in `${ARDUINO_SDK_PATH}/hardware/arduino/` lists all supported programmers by the *Arduino SDK*.

In order to enable programmer support, you have to use the **PROGRAMMER** option (see `Creating firmware images`_)::

    set(${TARGET_NAME}_PROGRAMMER programmer_id)

where `programmer_id` is the name of the programmer supported by the *Arduino SDK*.

Once you have enabled programmer support, two new targets are available in the build system:

* **${TARGET_NAME}-burn** - burns the firmware image via the programmer
* **${TARGET_NAME}-burn-bootloader** - burns the original **Arduino bootloader** image via the programmer

If you need to restore the original **Arduino bootloader** onto your Arduino, so that you can use the traditional way of uploading firmware images via the bootloader, use **${TARGET_NAME}-burn-bootloader** to restore it.

Pure AVR Development
~~~~~~~~~~~~~~~~~~~~

For those developers who don't want any Arduino magic, but still want to utilize the hardware platform you are in luck. This section will outline the `generate_avr_firmware()` and `generate_avr_library()` commands, which enables
you to compile sources for the given Arduino board.

No Arduino Core or Arduino libraries will get generated, this is for manual compilation of sources. These commands are for people that know what they are doing, or have done pure AVR development.
People starting out, or just familiar with Arduino should not use these commands.

The `generate_avr_firmware()` command::

    generate_avr_firmware(name
         [BOARD board_name]
         [BOARD_CPU board_cpu]
         [SRCS  src1 src2 ... srcN]
         [HDRS  hdr1 hdr2 ... hdrN]
         [LIBS  lib1 lib2 ... libN]
         [PORT  port]
         [SERIAL serial_cmd]
         [PROGRAMMER programmer_id]
         [AFLAGS flags])

This will compile the sources for the specified Arduino board type.

The options:

+--------------------+----------------------------------------------------------------------+----------------------------------------+
| **Name**           | **Description**                                                      | **REQUIRED**                           |
+--------------------+----------------------------------------------------------------------+----------------------------------------+
| **BOARD**          | Board name *(such as uno, mega2560, ...)*                            | **REQUIRED**                           |
+--------------------+----------------------------------------------------------------------+----------------------------------------+
| **BOARD_CPU**      | Board CPU *(such as atmega328, atmega168, ...)*                      | **REQUIRED** if board cpu is ambiguous |
+--------------------+----------------------------------------------------------------------+----------------------------------------+
| **SRCS**           | Source files                                                         | **REQUIRED**                           |
+--------------------+----------------------------------------------------------------------+----------------------------------------+
| **HDRS**           | Headers files *(for project based build systems)*                    |                                        |
+--------------------+----------------------------------------------------------------------+----------------------------------------+
| **LIBS**           | Libraries to link *(sets up dependency tracking)*                    |                                        |
+--------------------+----------------------------------------------------------------------+----------------------------------------+
| **PORT**           | Serial port, for upload and serial targets (see `Upload Firmware`_)  |                                        |
+--------------------+----------------------------------------------------------------------+----------------------------------------+
| **SERIAL**         | Serial command for serial target (see `Serial Terminal`_)            |                                        |
+--------------------+----------------------------------------------------------------------+----------------------------------------+
| **PROGRAMMER**     | Programmer ID, enables programmer burning (see `Programmers`_).      |                                        |
+--------------------+----------------------------------------------------------------------+----------------------------------------+
| **AFLAGS**         | avrdude flags for target                                             |                                        |
+--------------------+----------------------------------------------------------------------+----------------------------------------+

You can specify the options in two ways, either as the command arguments or as variables. When specifying the options as variables they must be named::

    ${TARGET_NAME}_${OPTION_NAME}

Where **${TARGET_NAME}** is the name of you target and **${OPTION_NAME}** is the name of the option.

The `generate_avr_library()` command::

    generate_avr_library(name
         [BOARD board_name]
         [BOARD_CPU board_cpu]
         [SRCS  src1 src2 ... srcN]
         [HDRS  hdr1 hdr2 ... hdrN]
         [LIBS  lib1 lib2 ... libN])

This will compile a static library for the specified Arduino board type.

The options:

+--------------------+---------------------------------------------------+----------------------------------------+
| **Name**           | **Description**                                   | **REQUIRED**                           |
+--------------------+---------------------------------------------------+----------------------------------------+
| **BOARD**          | Board name *(such as uno, mega2560, ...)*         | **REQUIRED**                           |
+--------------------+---------------------------------------------------+----------------------------------------+
| **BOARD_CPU**      | Board CPU *(such as atmega328, atmega168, ...)*   | **REQUIRED** if board cpu is ambiguous |
+--------------------+---------------------------------------------------+----------------------------------------+
| **SRCS**           | Source files                                      | **REQUIRED**                           |
+--------------------+---------------------------------------------------+----------------------------------------+
| **HDRS**           | Headers files *(for project based build systems)* |                                        |
+--------------------+---------------------------------------------------+----------------------------------------+
| **LIBS**           | Libraries to link *(sets up dependency tracking)* |                                        |
+--------------------+---------------------------------------------------+----------------------------------------+

You can specify the options in two ways, either as the command arguments or as variables. When specifying the options as variables they must be named::

    ${TARGET_NAME}_${OPTION_NAME}

Where **${TARGET_NAME}** is the name of you target and **${OPTION_NAME}** is the name of the option.

Register Custom Hardware Platforms
~~~~~~~~~~~~~~~~
Arduino development may involve the use of additional hardware platforms that behave differently, 
such as the Sagnuino e.g.
Arduino CMake allows you to register those platforms without the need to copy their files locally, 
exactly as you would register the default Arduino platform. In fact, this is what happens behind the scenes:

1. Platform's path is determined. By default it's Arduino's path. 
   See: `Arduino Platforms PRE 1.5`_ and `Arduino Platforms 1.5`_.

2. Platform's architecture is determined. By default it's avr.

If one would like to specify a custom platform and/or architecuture, it should set the following variables:

+--------------------------------+---------------------------------------------------+
| **Name**                       | **Description**                                   |
+--------------------------------+---------------------------------------------------+
| **PLATFORM_PATH**              | Platform's path on the local file system.*        |
+--------------------------------+---------------------------------------------------+
| **PLATFORM_ARCHITECTURE**      | Platform's architecture*                          |
+--------------------------------+---------------------------------------------------+

**Note:** If variables are to be used, they MUST be set before including the Toolchain file.
  
A valid Hardware Platform is a directory containing the following::
  
      HARDWARE_PLATFORM_PATH/
          |-- bootloaders/
          |-- cores/
          |-- variants/
          |-- boards.txt
          `-- programmers.txt
  
The ``board.txt`` describes the target boards and bootloaders, While ``programmers.txt`` the programmer defintions.
  
A good example of a *Hardware Platform* is in the Arduino SDK: ``${ARDUINO_SDK_PATH}/hardware/arduino/``
.. _Arduino Platforms PRE 1.5: http://code.google.com/p/arduino/wiki/Platforms
.. _Arduino Platforms 1.5: http://code.google.com/p/arduino/wiki/Platforms1

Advanced Options
~~~~~~~~~~~~~~~~

The following options control how **Arduino CMake** is configured:

+---------------------------------+-----------------------------------------------------+
| **Name**                        | **Description**                                     |
+---------------------------------+-----------------------------------------------------+
| **ARDUINO_SDK_PATH**            | Full path to the **Arduino SDK**                    |
+---------------------------------+-----------------------------------------------------+
| **ARDUINO_AVRDUDE_PROGRAM**     | Full path to `avrdude` programmer                   |
+---------------------------------+-----------------------------------------------------+
| **ARDUINO_AVRDUDE_CONFIG_PATH** | Full path to `avrdude` configuration file           |
+---------------------------------+-----------------------------------------------------+
| **ARDUINO_DEFAULT_BOARD**       | Default Arduino Board ID, when not specified.       |
+---------------------------------+-----------------------------------------------------+
| **ARDUINO_DEFAULT_PORT**        | Default Arduino port, when not specified.           |
+---------------------------------+-----------------------------------------------------+
| **ARDUINO_DEFAULT_SERIAL**      | Default Arduino Serial command, when not specified. |
+---------------------------------+-----------------------------------------------------+
| **ARDUINO_DEFAULT_PROGRAMMER**  | Default Arduino Programmer ID, when not specified.  |
+---------------------------------+-----------------------------------------------------+

To force a specific version of **Arduino SDK**, configure the project like so::

    cmake -DARDUINO_SDK_PATH=/path/to/arduino_sdk ../path/to/sources

Note: You must create a new build system if you change **ARDUINO_SDK_PATH**.

When **Arduino CMake** is configured properly, these options are defined:

+---------------------------------+-----------------------------------------------------+
| **Name**                        | **Description**                                     |
+---------------------------------+-----------------------------------------------------+
| **ARDUINO_FOUND**               | Set to True when the **Arduino SDK** is detected    |
|                                 | and configured.                                     |
+---------------------------------+-----------------------------------------------------+
| **ARDUINO_SDK_VERSION**         | Full version of the **Arduino SDK** (ex: 1.0.0)     |
+---------------------------------+-----------------------------------------------------+
| **ARDUINO_SDK_VERSION_MAJOR**   | Major version of the **Arduino SDK** (ex: 1)        |
+---------------------------------+-----------------------------------------------------+
| **ARDUINO_SDK_VERSION_MINOR**   | Minor version of the **Arduino SDK** (ex: 0)        |
+---------------------------------+-----------------------------------------------------+
| **ARDUINO_SDK_VERSION_PATCH**   | Patch version of the **Arduino SDK** (ex: 0)        |
+---------------------------------+-----------------------------------------------------+

During compilation, you can enable the following environment variables.

+---------------------------------+-----------------------------------------------------+
| **Name**                        | **Description**                                     |
+---------------------------------+-----------------------------------------------------+
| **VERBOSE**                     | Enables verbose compilation, displays commands      |
|                                 | being executed. (Non empty value)                   |
+---------------------------------+-----------------------------------------------------+
| **VERBOSE_SIZE**                | Enables full/verbose output from avr-size.          |
|                                 | (Non empty value)                                   |
+---------------------------------+-----------------------------------------------------+

Miscellaneous Functions
~~~~~~~~~~~~~~~~~~~~~~~

This section will outlines some of the additional miscellaneous functions available to the user.

* **print_board_list()**:
  
  Print list of detected Arduino Boards.
* **print_programmer_list()**:
  
  Print list of detected Programmers.
* **print_programmer_settings(PROGRAMMER)**:
  
     *PROGRAMMER* - programmer id
  
  Print the detected Programmer settings.
* **print_board_settings(BOARD_NAME)**:
  
    *BOARD_NAME* - Board name (nano, uno, mega...)
  
  Print the detected Arduino board settings.
  
Bundling Arduino CMake
~~~~~~~~~~~~~~~~~~~~~~

Using **Arduino CMake** in your own project is simple, you just need a single directory called **cmake**. Just copy that entire directory into you project and you are set.

Copying the **cmake** directory, although simple is not the best solution. If you are using GIT for source code versioning, the best solution is using a submodule. The submodule gives you the power of updating to the latest version of **Arduino CMake** without any effort. To add a submodule do::

    git submodule add git://github.com/queezythegreat/arduino-cmake.git arduino-cmake

Then just set the CMAKE_TOOLCHAIN_FILE variable::

    set(CMAKE_TOOLCHAIN_FILE ${CMAKE_SOURCE_DIR}/arduino-cmake/cmake/ArduinoToolchain.cmake)

For more information on GIT submodules please read: `GIT Book - Submodules`_

.. _GIT Book - Submodules: http://book.git-scm.com/5_submodules.html

Linux Environment
-----------------

Running the *Arduino SDK* on Linux is a little bit more involved, because not everything is bundled with the SDK. The AVR GCC toolchain is not distributed alongside the Arduino SDK, so it has to be installed seperately.

To get **Arduino CMake** up and running follow these steps:

1. Install the following packages using your package manager:
    
   * ``gcc-avr``      - AVR GNU GCC compiler
   * ``binutils-avr`` - AVR binary tools
   * ``avr-libc``     - AVR C library
   * ``avrdude``      - Firmware uploader
    
2. Install the *Arduino SDK*.
    
   Depending on your distribution, the *Arduino SDK* may or may not be available.
    
   If it is available please install it using your packages manager otherwise do:
    
   1. Download the `Arduino SDK`_
   2. Extract it into ``/usr/share``
    
   NOTE: Arduino version **0.19** or newer is required!

3. Install CMake:
    
   * Using the package manager or
   * Using the `CMake installer`_

   NOTE: CMake version 2.8 or newer is required!

Linux Serial Naming
~~~~~~~~~~~~~~~~~~~

On Linux the Arduino serial device is named as follows (where **X** is the device number)::

    /dev/ttyUSBX
    /dev/ttyACMX

Where ``/dev/ttyACMX`` is for the new **Uno** and **Mega** Arduino's, while ``/dev/ttyUSBX`` is for the old ones.

CMake configuration example::

    set(${FIRMWARE_NAME}_PORT /dev/ttyUSB0)

Linux Serial Terminals
~~~~~~~~~~~~~~~~~~~~~~

On Linux a wide range on serial terminal are availabe. Here is a list of a couple:

* ``minicom``
* ``picocom``
* ``gtkterm``
* ``screen``

Mac OS X Environment
--------------------

The *Arduino SDK*, as on Windows, is self contained and has everything needed for building. To get started do the following:

1. Install the  *Arduino SDK*

   1. Download `Arduino SDK`_
   2. Copy ``Arduino`` into ``Applications``
   3. Install ``FTDIUSBSerialDrviver*`` (for FTDI USB Serial)

2. Install CMake
   
   1. Download `CMake`_
   2. Install ``cmake-*.pkg``
        
      NOTE: Make sure to click on **`Install Command Line Links`**

Mac Serial Naming
~~~~~~~~~~~~~~~~~

When specifying the serial port name on Mac OS X, use the following names (where XXX is a unique ID)::

    /dev/tty.usbmodemXXX
    /dev/tty.usbserialXXX

Where ``tty.usbmodemXXX`` is for new **Uno** and **Mega** Arduino's, while ``tty.usbserialXXX`` are the older ones. 

CMake configuration example::

    set(${FIRMWARE_NAME}_PORT /dev/tty.usbmodem1d11)

Mac Serial Terminals
~~~~~~~~~~~~~~~~~~~~

On Mac the easiest way to get a Serial Terminal is to use the ``screen`` terminal emulator. To start a ``screen`` serial session::

    screen /dev/tty.usbmodemXXX

Where ``/dev/tty.usbmodemXXX`` is the terminal device. To exit press ``C-a C-\``.

CMake configuration example::

    set(${FIRMWARE_NAME}_SERIAL screen @SERIAL_PORT@)

Windows Environment
-------------------

On Windows the *Arduino SDK* is self contained and has everything needed for building. To setup the environment do the following:

1. Place the `Arduino SDK`_ either
   
   * into  **Program Files**, or
   * onto the **System Path**
    
   NOTE: Don't change the default *Arduino SDK* directory name, otherwise auto detection will no work properly!

2. Add to the **System Path**: ``${ARDUINO_SDK_PATH}/hardware/tools/avr/utils/bin``
3. Install `CMake 2.8`_
   
   NOTE: Make sure you check the option to add CMake to the **System Path**.

CMake Generators
~~~~~~~~~~~~~~~~

Once installed, you can start using CMake the usual way, just make sure to chose either a **MSYS Makefiles** or **Unix Makefiles** type generator::

    MSYS Makefiles              = Generates MSYS makefiles.
    Unix Makefiles              = Generates standard UNIX makefiles.
    CodeBlocks - Unix Makefiles = Generates CodeBlocks project files.
    Eclipse CDT4 - Unix Makefiles
                                = Generates Eclipse CDT 4.0 project files.

If you want to use a **MinGW Makefiles** type generator, you must generate the build system the following way:

1. Remove ``${ARDUINO_SDK_PATH}/hardware/tools/avr/utils/bin`` from the **System Path**
2. Generate the build system using CMake with the following option set (either through the GUI or from the command line)::

    CMAKE_MAKE_PROGRAM=${ARDIUNO_SDK_PATH}/hardware/tools/avr/utils/bin/make.exe

3. Then build the normal way

The reason for doing this is the MinGW generator cannot have the ``sh.exe`` binary on the **System Path** during generation, otherwise you get an error.

Windows Serial Naming
~~~~~~~~~~~~~~~~~~~~~

When specifying the serial port name on Windows, use the following names::

    com1 com2 ... comN

CMake configuration example::

    set(${FIRMWARE_NAME}_PORT com3)

Windows Serial Terminals
~~~~~~~~~~~~~~~~~~~~~~~~

Putty is a great multi-protocol terminal, which supports SSH, Telnet, Serial, and many more... The latest development snapshot supports command line options for launching a serial terminal, for example::

    putty -serial COM3 -sercfg 9600,8,n,1,X

CMake configuration example (assuming putty is on the **System Path**)::

    set(${FIRMWARE_NAME}_SERIAL putty -serial @SERIAL_PORT@)

Putty - http://tartarus.org/~simon/putty-snapshots/x86/putty-installer.exe

Eclipse Environment
-------------------

Eclipse is a great IDE which has a lot of functionality and is much more powerful than the *Arduino IDE*. In order to use Eclipse you will need the following:

1. Eclipse
2. Eclipse CDT extension (for C/C++ development)

On most Linux distribution you can install Eclipse + CDT using your package manager, otherwise you can download the `Eclipse IDE for C/C++ Developers`_ bundle.

Once you have Eclipse, here is how to generate a project using CMake:

1. Create a build directory that is next to your source directory, like this::
   
       build_directory/
       source_directory/

2. Run CMake with the `Eclipse CDT4 - Unix Makefiles` generator, inside the build directory::

        cd build_directory/
        cmake -G"Eclipse CDT4 - Unix Makefiles" ../source_directory

3. Open Eclipse and import the project from the build directory.

   1. **File > Import**
   2. Select `Existing Project into Workspace`, and click **Next**
   3. Select *Browse*, and select the build directoy.
   4. Select the project in the **Projects:** list
   5. Click **Finish**

.. _Eclipse IDE for C/C++ Developers: http://www.eclipse.org/downloads/packages/eclipse-ide-cc-developers/heliossr2

Troubleshooting
---------------

The following section will outline some solutions to common problems that you may encounter.

undefined reference to `__cxa_pure_virtual'
~~~~~~~~~~~~~~~~~~~~~~~~~~~~~~~~~~~~~~~~~~~

When linking you'r firmware image you may encounter this error on some systems. An easy fix is to add the following to your firmware source code::

    extern "C" void __cxa_pure_virtual(void);
    void __cxa_pure_virtual(void) { while(1); } 

The contents of the ``__cxa_pure_virtual`` function can be any error handling code; this function will be called whenever a pure virtual function is called. 

* `What is the purpose of `cxa_pure_virtual``_

.. _What is the purpose of `cxa_pure_virtual`: http://stackoverflow.com/questions/920500/what-is-the-purpose-of-cxa-pure-virtual

Arduino Mega 2560 image does not work
~~~~~~~~~~~~~~~~~~~~~~~~~~~~~~~~~~~~~

If you are working on Linux, and have ``avr-gcc`` >= 4.5 you might have a unpatched version gcc which has the C++ constructor bug. This bug affects the **Atmega2560** when using classes which causes the Arduino firmware to crash.

If you encounter this problem either downgrade ``avr-gcc`` to **4.3** or rebuild gcc with the following patch::

    --- gcc-4.5.1.orig/gcc/config/avr/libgcc.S  2009-05-23 17:16:07 +1000
    +++ gcc-4.5.1/gcc/config/avr/libgcc.S   2010-08-12 09:38:05 +1000
    @@ -802,7 +802,9 @@
        mov_h   r31, r29
        mov_l   r30, r28
        out     __RAMPZ__, r20
    +   push    r20
        XCALL   __tablejump_elpm__
    +   pop r20
     .L__do_global_ctors_start:
        cpi r28, lo8(__ctors_start)
        cpc r29, r17
    @@ -843,7 +845,9 @@
        mov_h   r31, r29
        mov_l   r30, r28
        out     __RAMPZ__, r20
    +   push    r20
        XCALL   __tablejump_elpm__
    +   pop r20
     .L__do_global_dtors_start:
        cpi r28, lo8(__dtors_end)
        cpc r29, r17

* `AVR GCC Bug 45263 Report`_
* `The global constructor bug in avr-gcc`_

.. _AVR GCC Bug 45263 Report: http://gcc.gnu.org/bugzilla/show_bug.cgi?id=45263
.. _The global constructor bug in avr-gcc: http://andybrown.me.uk/ws/2010/10/24/the-major-global-constructor-bug-in-avr-gcc/

Library not detected automatically
~~~~~~~~~~~~~~~~~~~~~~~~~~~~~~~~~~

When a Arduino library does not get detected automatically, it usually means CMake cannot find it (obvious).

One common reason why the library is not detected, is because the directory name of the library does not match the header.
If I'm including a library header like so::

    #include "my_library.h"

Based on this include, **Arduino CMake** is expecting to find a library that has a directory name **my_libray**.
If the directory name does not match the header, it won't be consider a Arduino Library (see `Arduino Libraries`_).

When a library being used is located in a non-standard location (not in the **Arduino SDK** or next to the firmware), then that directory must be registered.
To register a non-standard directory containing Arduino libraries, use the following::

    link_directories(path_to_directory_containing_libraries)

Remember to **use this command before defining the firmware**, which requires the library from that directory.

error: attempt to use poisoned "SIG_USART0_RECV"
~~~~~~~~~~~~~~~~~~~~~~~~~~~~~~~~~~~~~~~~~~~~~~~~

If you get the following error::

    /usr/share/arduino/hardware/arduino/cores/arduino/HardwareSerial.cpp:91:41: error: attempt to use poisoned "SIG_USART0_RECV"
    /usr/share/arduino/hardware/arduino/cores/arduino/HardwareSerial.cpp:101:15: error: attempt to use poisoned "SIG_USART0_RECV"
    /usr/share/arduino/hardware/arduino/cores/arduino/HardwareSerial.cpp:132:15: error: attempt to use poisoned "SIG_USART1_RECV"
    /usr/share/arduino/hardware/arduino/cores/arduino/HardwareSerial.cpp:145:15: error: attempt to use poisoned "SIG_USART2_RECV"
    /usr/share/arduino/hardware/arduino/cores/arduino/HardwareSerial.cpp:158:15: error: attempt to use poisoned "SIG_USART3_RECV"

You probably recently upgraded `avr-libc` to the latest version, which has deperecated the use of these symbols. There is a `Arduino Patch`_ which
fixes these error, you can read more about this bug here: `Arduino Bug ISSUE 955`_.

.. _Arduino Bug ISSUE 955: http://code.google.com/p/arduino/issues/detail?id=955
.. _Arduino Patch: http://arduino.googlecode.com/issues/attachment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

Resources
---------

Here are some resources you might find useful in getting started.

1. CMake:

   * `Offical CMake Tutorial`_
   * `CMake Tutorial`_
   * `CMake Reference`_

.. _Offical CMake Tutorial: http://www.cmake.org/cmake/help/cmake_tutorial.html
.. _CMake Tutorial: http://mathnathan.com/2010/07/11/getting-started-with-cmake/
.. _CMake Reference: http://www.cmake.org/cmake/help/cmake-2-8-docs.html

2. Arduino:
   
   * `Getting Started`_ - Introduction to Arduino
   * `Playground`_ - User contributed documentation and help
   * `Arduino Forums`_ - Official forums
   * `Arduino Reference`_ - Official reference manual

.. _Getting Started: http://www.arduino.cc/en/Guide/HomePage
.. _Playground: http://www.arduino.cc/playground/
.. _Arduino Reference: http://www.arduino.cc/en/Reference/HomePage
.. _Arduino Forums: http://www.arduino.cc/forum/

.. _CMake 2.8: http://www.cmake.org/cmake/resources/software.html
.. _CMake: http://www.cmake.org/cmake/resources/software.html
.. _CMake Installer: http://www.cmake.org/cmake/resources/software.html
.. _Arduino SDK: http://www.arduino.cc/en/Main/Software

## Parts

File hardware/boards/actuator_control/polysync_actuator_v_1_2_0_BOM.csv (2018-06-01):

Polysync Actuator Board BOM V1.2.0
Quantity | Reference Designator | Description | Mfg | Mfg Part No. | Distributor | Distributor Part No. | Price | Total Price
8 | R7, R8, R11, R12, R25, R26, R27, R28 | RES SMD 0.02 OHM 1% 1W 1206 | Panasonic Electronic Components | ERJ-8CWFR020V | Digikey | P0.02BVCT-ND | 0.69 | 5.52
1 | R101 | RES SMD 0.3 OHM 1% 1/6W 0402 | Panasonic Electronic Components | ERJ-2BQFR30X | Digikey | P.30AKCT-ND | 0.59 | 0.59
5 | R106, R107, R108, R109, R110 | RES SMD 0.0OHM JUMPER 1/10W 0402 | Panasonic Electronic Components | ERJ-2GE0R00X | Digikey | P0.0JCT-ND | 0.1 | 0.5
8 | R9, R10, R15, R16, R29, R30, R31, R32 | RES SMD 0.0 OHM JUMPER 1/8W 0805 | Panasonic Electronic Components | ERJ-6GEY0R00V | Digikey | P0.0ACT-ND | 0.1 | 0.8
8 | R3, R4, R5, R6, R21, R22, R23, R24 | RES SMD 100 OHM 1% 1/8W 0805 | Panasonic Electronic Components | ERJ-6ENF1000V | Digikey | P100CCT-ND | 0.1 | 0.8
24 | R33, R34, R35, R45, R46, R47, R48, R49, R50, R57, R61, R62, R65, R66, R67, R77, R78, R79, R80, R81, R82, R89, R93, R94 | RES SMD 100K OHM 1% 1/10W 0402 | Panasonic Electronic Components | ERJ-2RKF1003X | Digikey | P100KLCT-ND | 0.1 | 2.4
10 | R1, R2, R13, R14, R17, R18, R19, R20, R104, R121 | RES SMD 10K OHM 1% 1/10W 0402 | Panasonic Electronic Components | ERJ-2RKF1002X | Digikey | P10.0KLCT-ND | 0.1 | 1
1 | R102 | RES SMD 120 OHM 1% 1/10W 0402 | Panasonic Electronic Components | ERJ-2RKF1200X | Digikey | P120LCT-ND | 0.1 | 0.1
48 | R36, R37, R38, R39, R40, R41, R42, R43, R44, R51, R52, R53, R54, R55, R56, R58, R59, R60, R63, R64, R68, R69, R70, R71, R72, R73, R74, R75, R76, R83, R84, R85, R86, R87, R88, R90, R91, R92, R95, R96, R97, R98, R99, R100, R103, R116, R117, R119 | RES SMD 1K OHM 1% 1/10W 0402 | Panasonic Electronic Components | ERJ-2RKF1001X | Digikey | P1.00KLCT-ND | 0.1 | 4.8
2 | R105, R120 | RES SMD 47K OHM 1% 1/10W 0402 | Panasonic Electronic Components | ERJ-2RKF4702X | Digikey | P47.0KLCT-ND | 0.1 | 0.2
1 | R118 | RES SMD 5.1K OHM 1% 1/10W 0402 | Panasonic Electronic Components | ERJ-2RKF5101X | Digikey | P5.10KLCT-ND | 0.1 | 0.1
18 | C26, C27, C29, C30, C32, C33, C35, C36, C38, C39, C41, C42, C44, C45, C47, C48, C49, C51 | 0.10µF ±10% 100V Ceramic Capacitor X5R 0402 (1005 Metric) | Murata Electronics North America | GRM155R62A104KE14D | Digikey | 490-10458-1-ND | 0.1 | 1.8
12 | C3, C4, C7, C8, C11, C12, C19, C20, C21, C22, C23, C24 | 0.10µF ±10% 100V Ceramic Capacitor X7R 0805 (2012 Metric) | Samsung Electro-Mechanics America, Inc. | CL21B104KCFNNNE | Digikey | 1276-6840-1-ND | 0.1 | 1.2
8 | C25, C28, C31, C34, C37, C40, C43, C46 | 100pF ±5% 50V Ceramic Capacitor C0G, NP0 0402 (1005 Metric) | Yageo | CC0402JRNPO9BN101 | Digikey | 311-1024-1-ND | 0.1 | 0.8
12 | C1, C2, C5, C6, C9, C10, C13, C14, C15, C16, C17, C18 | 1µF ±10% 100V Ceramic Capacitor X7R 1206 (3216 Metric) | Samsung Electro-Mechanics America, Inc. | CL31B105KCHNNNE | Digikey | 1276-1838-1-ND | 0.29 | 3.48
2 | C52, C53 | 22pF ±5% 50V Ceramic Capacitor C0G, NP0 0402 (1005 Metric) | Murata Electronics North America | GRM1555C1H220JA01J | Digikey | 490-11382-1-ND | 0.1 | 0.2
1 | C50 | 33µF ±10% Molded Tantalum Capacitors 10V 1206 (3216 Metric) 1.7 Ohm | AVX Corporation | TAJA336K010RNJ | Digikey | 478-8882-1-ND | 0.6 | 0.6
3 | Q9, Q11, Q12 | MOSFET N-CH 60V 6A | Toshiba Semiconductor and Storage | SSM3K341R,LF | Digikey | SSM3K341RLFCT-ND | 0.43 | 1.29
8 | Q1, Q2, Q3, Q4, Q5, Q6, Q7, Q8 | MOSFET N-CH 60V 50A 8SON | Texas Instruments | CSD18537NQ5A | Digikey | 296-36455-1-ND | 0.85 | 6.8
1 | Q10 | MOSFET N-CH 20V 0.2A EMT3 | Rohm Semiconductor | RE1C002UNTCL | Digikey | RE1C002UNTCLCT-ND | 0.2 | 0.2
1 | D21 | Blue 470nm LED Indication - Discrete 3.2V 0603 (1608 Metric) | Wurth Electronics Inc | 150060BS75000 | Digikey | 732-4966-1-ND | 0.26 | 0.26
2 | D17, D20 | LED RED CLEAR 0603 SMD | Wurth Electronics Inc | 150060RS75000 | Digikey | 732-4978-1-ND | 0.24 | 0.48
2 | D18, D19 | LED GREEN CLEAR 0603 SMD | Wurth Electronics Inc | 150060GS75000 | Digikey | 732-4971-1-ND | 0.24 | 0.48
8 | D1, D2, D3, D4, D5, D6, D7, D8 | Diode Standard 100V 1A Surface Mount SMA | Diodes Incorporated | US1B-13-F | Digikey | US1B-FDICT-ND | 0.42 | 3.36
8 | D9, D10, D11, D12, D13, D14, D15, D16 | Diode Schottky 20V 500mA Surface Mount SOD-123 | Diodes Incorporated | B0520LW-7-F | Digikey | B0520LW-FDICT-ND | 0.32 | 2.56
8 | L1, L2, L3, L4, L5, L6, L7, L8 | 2.2µH Shielded Wirewound Inductor 10A 12 mOhm Max Nonstandard | Bourns Inc. | SRP7050TA-2R2M | Digikey | SRP7050TA-2R2MCT-ND | 1.18 | 9.44
1 | X1 | 16MHz ±30ppm Crystal 18pF 40 Ohm -40°C ~ 85°C Surface Mount HC49/US | Abracon LLC | ABLS-16.000MHZ-D-4-T | Digikey | 535-13436-1-ND | 0.24 | 0.24
1 | U15 | CAN Controller CAN 2.0 SPI Interface 18-SOIC | Microchip Technology | MCP2515-I/SO | Digikey | MCP2515-I/SO-ND | 1.82 | 1.82
1 | U14 | 1/1 Transceiver Half CAN 8-SOIC | Microchip Technology | MCP2551-I/SN | Digikey | MCP2551-I/SN-ND | 1.02 | 1.02
8 | U5, U6, U7, U8, U9, U10, U11, U12 | General Purpose Amplifier 1 Circuit Rail-to-Rail SOT-23-5 | Texas Instruments | OPA170AIDBVT | Digikey | 296-29496-1-ND | 1.41 | 11.28
1 | U13 | Linear Voltage Regulator IC Positive Fixed 1 Output 5V 750mA DDPAK/TO-263-3 | Texas Instruments | TL750M05CKTTR | Digikey | 296-20776-1-ND | 1.47 | 1.47
4 | U1, U2, U3, U4 | Low-Side Gate Driver IC Non-Inverting 8-SOIC | Texas Instruments | UCC27524DR | Digikey | 296-30129-1-ND | 1.94 | 7.76
1 | RELAY1 | General Purpose Relay DPDT (2 Form C) Surface Mount | Kemet | EE2-5NU-L | Digikey | 399-11017-1-ND | 1.91 | 1.91
1 | RELAY2 | Automotive Relay SPDT (1 Form C) 12VDC Coil Through Hole | TE Connectivity Potter & Brumfield Relays | 1432868-1 | Digikey | PB1040-ND | 3.46 | 3.46
1 | RELAY3 | Relay Socket Through Hole | TE Connectivity Potter & Brumfield Relays | VCF4-1000 | Digikey | PB232-ND | 1.8 | 1.8
1 | JP2 | 2 Positions Header, Unshrouded Connector 0.100" (2.54mm) Through Hole Gold or Gold, GXT™ | Amphenol FCI | 77311-118-02LF | Digikey | 609-4434-ND | 0.18 | 0.18
1 | JP1 | 10 Positions Header, Unshrouded Connector 0.100" (2.54mm) Through Hole Gold | Wurth Electronics Inc | 61301011121 | Digikey | 732-2670-ND | 1.01 | 1.01
1 | XIO | 36 Positions Header, Unshrouded Connector 0.100" (2.54mm) Through Hole Gold | Wurth Electronics Inc | 61303621121 | Digikey | 732-5309-ND | 1.64 | 1.64
5 | ADCH, ADCL, COMMUNICATION, POWER, PWML | 8 Positions Header, Unshrouded Connector 0.100" (2.54mm) Through Hole Gold | Wurth Electronics Inc | 61300811121 | Digikey | 732-5321-ND | 0.35 | 1.75
2 | CON11, CON17 | 2 Position Wire to Board Terminal Block Horizontal with Board 0.400" (10.16mm) Through Hole | Phoenix Contact | 1773976 | Digikey | 277-5761-ND | 8.66 | 17.32
11 | CON1, CON2, CON3, CON4, CON5, CON6, CON7, CON8, CON12, CON14, CON16 | 2 Position Wire to Board Terminal Block 45° (135°) Angle with Board 0.138" (3.50mm) Through Hole | Phoenix Contact | 1988956 | Digikey | 277-1779-ND | 0.41 | 4.51
3 | CON9, CON10, CON13 | 3 Position Wire to Board Terminal Block 45° (135°) Angle with Board 0.138" (3.50mm) Through Hole | Phoenix Contact | 1988969 | Digikey | 277-1780-ND | 0.61 | 1.83
1 | CON15 | 5 Position Wire to Board Terminal Block 45° (135°) Angle with Board 0.138" (3.50mm) Through Hole | Phoenix Contact | 1988985 | Digikey | 277-1782-ND | 0.97 | 0.97
2 | F1, F3 | Fuse Holder 80V 1 Circuit Blade PCB | Littelfuse Inc. | 178.6165.0001 | Digikey | F5197-ND | 3.24 | 6.48
1 | For F3 | FUSE AUTO 40A 32VDC BLADE | Littelfuse Inc. | 0257040.PXAPC | Digikey | F5952-ND | 0.47 | 0.47
1 | For F1 | FUSE AUTOMOTIVE 20A 32VDC BLADE | Littelfuse Inc. | 0287020.PXCN | Digikey | F4201-ND | 0.28 | 0.28
1 | For JP2 | 2 (1 x 2) Position Shunt Connector White Open Top 0.100" (2.54mm) Gold or Gold, GXT™ | Amphenol FCI | 68786-102LF | Digikey | 609-3121-ND | 0.19 | 0.19
Total |  |  |  |  |  |  |  | $117.15

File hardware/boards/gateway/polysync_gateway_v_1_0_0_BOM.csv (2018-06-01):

Polysync Gateway Board BOM V1.0.0
Quantity | Reference Designator | Description | Mfg | Mfg Part No. | Distributor | Distributor Part No. | Price | Total Price
1 | R8 | RES SMD 0.3 OHM 1% 1/6W 0402 | Panasonic Electronic Components | ERJ-2BQFR30X | Digikey | P.30AKCT-ND | 0.59 | 0.59
10 | R2, R3, R9, R16, R17, R18, R19, R20, R21, R22 | RES SMD 10K OHM 1% 1/10W 0402 | Panasonic Electronic Components | ERJ-2RKF1002X | Digikey | P10.0KLCT-ND | 0.1 | 1
2 | R13, R15 | RES SMD 120 OHM 1% 1/10W 0402 | Panasonic Electronic Components | ERJ-2RKF1200X | Digikey | P120LCT-ND | 0.1 | 0.2
7 | R4, R5, R6, R7, R10, R11, R12 | RES SMD 1K OHM 1% 1/10W 0402 | Panasonic Electronic Components | ERJ-2RKF1001X | Digikey | P1.00KLCT-ND | 0.1 | 0.7
2 | R1, R14 | RES SMD 47K OHM 1% 1/10W 0402 | Panasonic Electronic Components | ERJ-2RKF4702X | Digikey | P47.0KLCT-ND | 0.1 | 0.2
4 | C1, C2, C6, C9 | 0.10µF ±10% 16V Ceramic Capacitor X7R 0402 (1005 Metric) | Murata Electronics North America | GRM155R71C104KA88J | Digikey | 490-6328-1-ND | 0.1 | 0.4
4 | C4, C5, C7, C8 | 22pF ±5% 50V Ceramic Capacitor C0G, NP0 0402 (1005 Metric) | Murata Electronics North America | GRM1555C1H220JA01J | Digikey | 490-11382-1-ND | 0.1 | 0.4
1 | C3 | 33µF ±10% Molded Tantalum Capacitors 10V 1206 (3216 Metric) 1.7 Ohm | AVX Corporation | TAJA336K010RNJ | Digikey | 478-8882-1-ND | 0.6 | 0.6
2 | D5, D8 | Blue 470nm LED Indication - Discrete 3.2V 0603 (1608 Metric) | Wurth Electronics Inc | 150060BS75000 | Digikey | 732-4966-1-ND | 0.26 | 0.52
2 | D4, D7 | LED RED CLEAR 0603 SMD | Wurth Electronics Inc | 150060RS75000 | Digikey | 732-4978-1-ND | 0.24 | 0.48
3 | D2, D3, D6 | LED GREEN CLEAR 0603 SMD | Wurth Electronics Inc | 150060GS75000 | Digikey | 732-4971-1-ND | 0.24 | 0.72
2 | X1, X2 | 16MHz ±30ppm Crystal 18pF 40 Ohm -40°C ~ 85°C Surface Mount HC49/US | Abracon LLC | ABLS-16.000MHZ-D-4-T | Digikey | 535-13436-1-ND | 0.24 | 0.48
2 | U2, U5 | CAN Controller CAN 2.0 SPI Interface 18-SOIC | Microchip Technology | MCP2515-I/SO | Digikey | MCP2515-I/SO-ND | 1.82 | 3.64
2 | U1, U3 | 1/1 Transceiver Half CAN 8-SOIC | Microchip Technology | MCP2551-I/SN | Digikey | MCP2551-I/SN-ND | 1.02 | 2.04
1 | U4 | Linear Voltage Regulator IC Positive Fixed 1 Output 5V 750mA DDPAK/TO-263-3 | Texas Instruments | TL750M05CKTTR | Digikey | 296-20776-1-ND | 1.47 | 1.47
1 | U6 | IC BUFF/DVR TRI-ST DUAL 20TSSOP | Texas Instruments | SN74AC241PWR | Digikey | 296-4309-1-ND | 0.75 | 0.75
1 | JP1 | 10 Positions Header, Unshrouded Connector 0.100" (2.54mm) Through Hole Gold or Gold, GXT™ | Amphenol FCI | 68002-210HLF | Digikey | 609-3301-ND | 0.44 | 0.44
2 | JP2, JP5 | 8 Positions Header, Unshrouded Connector 0.100" (2.54mm) Through Hole Gold or Gold, GXT™ | Amphenol FCI | 68000-208HLF | Digikey | 609-3257-ND | 0.43 | 0.86
1 | JP3 | 6 Position Receptacle Connector 0.100" (2.54mm) Through Hole Gold | Amphenol FCI | 68683-303LF | Digikey | 609-3582-ND | 1.61 | 1.61
1 | JP4 | 6 Positions Header, Unshrouded Connector 0.100" (2.54mm) Through Hole Gold or Gold, GXT™ | Amphenol FCI | 68000-206HLF | Digikey | 609-3256-ND | 0.32 | 0.32
2 | JP6, JP7 | 2 Positions Header, Unshrouded Connector 0.100" (2.54mm) Through Hole Gold or Gold, GXT™ | Amphenol FCI | 77311-118-02LF | Digikey | 609-4434-ND | 0.18 | 0.36
3 | CON1, CON2, CON3 | 2 Position Wire to Board Terminal Block 45° (135°) Angle with Board 0.138" (3.50mm) Through Hole | Phoenix Contact | 1988956 | Digikey | 277-1779-ND | 0.41 | 1.23
1 | CON4 | CONN HEADER PH SIDE 8POS 2MM SMD | JST Sales America Inc. | S8B-PH-SM4-TB(LF)(SN) | Digikey | 455-1755-1-ND | 0.97 | 0.97
2 | For JP6, JP7 | 2 (1 x 2) Position Shunt Connector White Open Top 0.100" (2.54mm) Gold or Gold, GXT™ | Amphenol FCI | 68786-102LF | Digikey | 609-3121-ND | 0.19 | 0.38
Total |  |  |  |  |  |  |  | $20.36

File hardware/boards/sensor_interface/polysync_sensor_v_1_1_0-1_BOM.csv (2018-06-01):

Polysync Sensor BOM v1.1.0
Quantity | Reference Designator | Description | Mfg | Mfg Part No. | Distributor | Distributor Part No. | Price | Total Price
1 | R8 | RES SMD 0.3 OHM 1% 1/6W 0402 | Panasonic Electronic Components | ERJ-2BQFR30X | Digikey | P.30AKCT-ND | 0.59 | 0.59
5 | R3, R15, R16, R19, R20 | RES SMD 0.0OHM JUMPER 1/10W 0402 | Panasonic Electronic Components | ERJ-2GE0R00X | Digikey | P0.0JCT-ND | 0.1 | 0.5
6 | R2, R9, R11, R17, R18, R23 | RES SMD 10K OHM 1% 1/10W 0402 | Panasonic Electronic Components | ERJ-2RKF1002X | Digikey | P10.0KLCT-ND | 0.1 | 0.6
1 | R13 | RES SMD 120 OHM 1% 1/10W 0402 | Panasonic Electronic Components | ERJ-2RKF1200X | Digikey | P120LCT-ND | 0.1 | 0.1
5 | R1, R4, R5, R6, R7 | RES SMD 1K OHM 1% 1/10W 0402 | Panasonic Electronic Components | ERJ-2RKF1001X | Digikey | P1.00KLCT-ND | 0.1 | 0.5
1 | R14 | RES SMD 47K OHM 1% 1/10W 0402 | Panasonic Electronic Components | ERJ-2RKF4702X | Digikey | P47.0KLCT-ND | 0.1 | 0.1
4 | C1, C2, C6, C8 | 0.10µF ±10% 16V Ceramic Capacitor X7R 0402 (1005 Metric) | Murata Electronics North America | GRM155R71C104KA88J | Digikey | 490-6328-1-ND | 0.1 | 0.4
3 | C5, C9, C19 | 10µF ±10% 10V Ceramic Capacitor X7R 0805 (2012 Metric) | Taiyo Yuden | LMK212B7106KG-TD | Digikey | 587-2668-1-ND | 0.28 | 0.84
2 | C4, C7 | 22pF ±5% 50V Ceramic Capacitor C0G, NP0 0402 (1005 Metric) | Murata Electronics North America | GRM1555C1H220JA01J | Digikey | 490-11382-1-ND | 0.1 | 0.2
1 | C3 | 33µF ±10% Molded Tantalum Capacitors 10V 1206 (3216 Metric) 1.7 Ohm | AVX Corporation | TAJA336K010RNJ | Digikey | 478-8882-1-ND | 0.6 | 0.6
1 | D5 | Blue 470nm LED Indication - Discrete 3.2V 0603 (1608 Metric) | Wurth Electronics Inc | 150060BS75000 | Digikey | 732-4966-1-ND | 0.26 | 0.26
2 | D1, D4 | LED RED CLEAR 0603 SMD | Wurth Electronics Inc | 150060RS75000 | Digikey | 732-4978-1-ND | 0.24 | 0.48
2 | D2, D3 | LED GREEN CLEAR 0603 SMD | Wurth Electronics Inc | 150060GS75000 | Digikey | 732-4971-1-ND | 0.24 | 0.48
1 | X1 | 16MHz ±30ppm Crystal 18pF 40 Ohm -40°C ~ 85°C Surface Mount HC49/US | Abracon LLC | ABLS-16.000MHZ-D-4-T | Digikey | 535-13436-1-ND | 0.24 | 0.24
1 | Q1 | MOSFET N-CH 20V 0.2A EMT3 | Rohm Semiconductor | RE1C002UNTCL | Digikey | RE1C002UNTCLCT-ND | 0.2 | 0.2
1 | U2 | CAN Controller CAN 2.0 SPI Interface 18-SOIC | Microchip Technology | MCP2515-I/SO | Digikey | MCP2515-I/SO-ND | 1.82 | 1.82
1 | U1 | 1/1 Transceiver Half CAN 8-SOIC | Microchip Technology | MCP2551-I/SN | Digikey | MCP2551-I/SN-ND | 1.02 | 1.02
1 | U5 | 12 Bit Digital to Analog Converter 2 14-TSSOP | Microchip Technology | MCP4922T-E/ST | Digikey | MCP4922T-E/STCT-ND | 2.62 | 2.62
1 | U4 | Linear Voltage Regulator IC Positive Fixed 1 Output 5V 750mA DDPAK/TO-263-3 | Texas Instruments | TL750M05CKTTR | Digikey | 296-20776-1-ND | 1.47 | 1.47
1 | U6 | IC SWITCH BUS DUAL FET 8-SOIC | Texas Instruments | SN74CBT3306CDR | Digikey | 296-19215-1-ND | 0.6 | 0.6
1 | RELAY1 | General Purpose Relay DPDT (2 Form C) Surface Mount | Kemet | EE2-5NU-L | Digikey | 399-11017-1-ND | 1.91 | 1.91
1 | JP1 | 10 Positions Header, Unshrouded Connector 0.100" (2.54mm) Through Hole Gold or Gold, GXT™ | Amphenol FCI | 68002-210HLF | Digikey | 609-3301-ND | 0.44 | 0.44
2 | JP2, JP5 | 8 Positions Header, Unshrouded Connector 0.100" (2.54mm) Through Hole Gold or Gold, GXT™ | Amphenol FCI | 68000-208HLF | Digikey | 609-3257-ND | 0.43 | 0.86
1 | JP3 | 6 Position Receptacle Connector 0.100" (2.54mm) Through Hole Gold | Amphenol FCI | 68683-303LF | Digikey | 609-3582-ND | 1.61 | 1.61
1 | JP4 | 6 Positions Header, Unshrouded Connector 0.100" (2.54mm) Through Hole Gold or Gold, GXT™ | Amphenol FCI | 68000-206HLF | Digikey | 609-3256-ND | 0.32 | 0.32
1 | JP6 | 2 Positions Header, Unshrouded Connector 0.100" (2.54mm) Through Hole Gold or Gold, GXT™ | Amphenol FCI | 77311-118-02LF | Digikey | 609-4434-ND | 0.18 | 0.18
2 | CON1, CON2 | 2 Position Wire to Board Terminal Block 45° (135°) Angle with Board 0.138" (3.50mm) Through Hole | Phoenix Contact | 1988956 | Digikey | 277-1779-ND | 0.41 | 0.82
2 | CON3, CON4 | 4 Position Wire to Board Terminal Block 45° (135°) Angle with Board 0.138" (3.50mm) Through Hole | Phoenix Contact | 1988972 | Digikey | 277-1781-ND | 0.82 | 1.64
1 | For JP6 | 2 (1 x 2) Position Shunt Connector White Open Top 0.100" (2.54mm) Gold or Gold, GXT™ | Amphenol FCI | 68786-102LF | Digikey | 609-3121-ND | 0.19 | 0.19
Total |  |  |  |  |  |  |  | $21.59

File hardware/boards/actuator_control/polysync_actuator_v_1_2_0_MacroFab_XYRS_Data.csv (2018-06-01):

# Generated by MacroFab for PCB 0yg5f4, version 1.
# DESIGNATOR | X_LOC | Y_LOC | ROTATION | SIDE | TYPE | X_SIZE | Y_SIZE | VALUE | FOOTPRINT | POPULATE | MPN | MPN1 | MPN2 | MPN3
ADCH | 3810 | 2170 | 0 | 2 | 2 | 733.46 | 33.46 | 8x1F-H8.5 | 1X08 | 1 |  |  |  |  | 61300811121
ADCL | 2910 | 2170 | 0 | 2 | 2 | 733.46 | 33.46 | 8x1F-H8.5 | 1X08 | 1 |  |  |  |  | 61300811121
C1 | 1760 | 1045 | 0 | 2 | 1 | 149.61 | 62.99 | 1u | C1206 | 1 |  |  |  |  | CL31B105KCHNNNE
C10 | 6185 | 1045 | 0 | 2 | 1 | 149.61 | 62.99 | 1u | C1206 | 1 |  |  |  |  | CL31B105KCHNNNE
C11 | 510 | 770 | 270 | 2 | 1 | 102.36 | 51.18 | 0.1u | C0805 | 1 |  |  |  |  | CL21B104KCFNNNE
C12 | 3560 | 770 | 270 | 2 | 1 | 102.36 | 51.18 | 0.1u | C0805 | 1 |  |  |  |  | CL21B104KCFNNNE
C13 | 760 | 5145 | 180 | 2 | 1 | 149.61 | 62.99 | 1u | C1206 | 1 |  |  |  |  | CL31B105KCHNNNE
C14 | 2235 | 5145 | 180 | 2 | 1 | 149.61 | 62.99 | 1u | C1206 | 1 |  |  |  |  | CL31B105KCHNNNE
C15 | 3710 | 5145 | 180 | 2 | 1 | 149.61 | 62.99 | 1u | C1206 | 1 |  |  |  |  | CL31B105KCHNNNE
C16 | 5185 | 5145 | 180 | 2 | 1 | 149.61 | 62.99 | 1u | C1206 | 1 |  |  |  |  | CL31B105KCHNNNE
C17 | 3485 | 5420 | 90 | 2 | 1 | 149.61 | 62.99 | 1u | C1206 | 1 |  |  |  |  | CL31B105KCHNNNE
C18 | 6460 | 5420 | 90 | 2 | 1 | 149.61 | 62.99 | 1u | C1206 | 1 |  |  |  |  | CL31B105KCHNNNE
C19 | 1760 | 4820 | 180 | 2 | 1 | 102.36 | 51.18 | 0.1u | C0805 | 1 |  |  |  |  | CL21B104KCFNNNE
C2 | 3235 | 1045 | 0 | 2 | 1 | 149.61 | 62.99 | 1u | C1206 | 1 |  |  |  |  | CL31B105KCHNNNE
C20 | 3235 | 4820 | 180 | 2 | 1 | 102.36 | 51.18 | 0.1u | C0805 | 1 |  |  |  |  | CL21B104KCFNNNE
C21 | 4710 | 4820 | 180 | 2 | 1 | 102.36 | 51.18 | 0.1u | C0805 | 1 |  |  |  |  | CL21B104KCFNNNE
C22 | 6185 | 4820 | 180 | 2 | 1 | 102.36 | 51.18 | 0.1u | C0805 | 1 |  |  |  |  | CL21B104KCFNNNE
C23 | 3385 | 5420 | 90 | 2 | 1 | 102.36 | 51.18 | 0.1u | C0805 | 1 |  |  |  |  | CL21B104KCFNNNE
C24 | 6360 | 5420 | 90 | 2 | 1 | 102.36 | 51.18 | 0.1u | C0805 | 1 |  |  |  |  | CL21B104KCFNNNE
C25 | 585 | 1445 | 180 | 2 | 1 | 62.99 | 23.62 | 100p | C0402 | 1 |  |  |  |  | CC0402JRNPO9BN101
C26 | 460 | 1720 | 270 | 2 | 1 | 62.99 | 23.62 | .1u | C0402 | 1 |  |  |  |  | GRM155R62A104KE14D
C27 | 560 | 1770 | 90 | 2 | 1 | 62.99 | 23.62 | .1u | C0402 | 1 |  |  |  |  | GRM155R62A104KE14D
C28 | 2060 | 1445 | 180 | 2 | 1 | 62.99 | 23.62 | 100p | C0402 | 1 |  |  |  |  | CC0402JRNPO9BN101
C29 | 1935 | 1720 | 270 | 2 | 1 | 62.99 | 23.62 | .1u | C0402 | 1 |  |  |  |  | GRM155R62A104KE14D
C3 | 3710 | 1370 | 0 | 2 | 1 | 102.36 | 51.18 | 0.1u | C0805 | 1 |  |  |  |  | CL21B104KCFNNNE
C30 | 2035 | 1770 | 90 | 2 | 1 | 62.99 | 23.62 | .1u | C0402 | 1 |  |  |  |  | GRM155R62A104KE14D
C31 | 3535 | 1445 | 180 | 2 | 1 | 62.99 | 23.62 | 100p | C0402 | 1 |  |  |  |  | CC0402JRNPO9BN101
C32 | 3410 | 1720 | 270 | 2 | 1 | 62.99 | 23.62 | .1u | C0402 | 1 |  |  |  |  | GRM155R62A104KE14D
C33 | 3510 | 1770 | 90 | 2 | 1 | 62.99 | 23.62 | .1u | C0402 | 1 |  |  |  |  | GRM155R62A104KE14D
C34 | 5010 | 1445 | 180 | 2 | 1 | 62.99 | 23.62 | 100p | C0402 | 1 |  |  |  |  | CC0402JRNPO9BN101
C35 | 4885 | 1720 | 270 | 2 | 1 | 62.99 | 23.62 | .1u | C0402 | 1 |  |  |  |  | GRM155R62A104KE14D
C36 | 4985 | 1770 | 90 | 2 | 1 | 62.99 | 23.62 | .1u | C0402 | 1 |  |  |  |  | GRM155R62A104KE14D
C37 | 1935 | 4745 | 0 | 2 | 1 | 62.99 | 23.62 | 100p | C0402 | 1 |  |  |  |  | CC0402JRNPO9BN101
C38 | 2060 | 4470 | 90 | 2 | 1 | 62.99 | 23.62 | .1u | C0402 | 1 |  |  |  |  | GRM155R62A104KE14D
C39 | 1960 | 4420 | 270 | 2 | 1 | 62.99 | 23.62 | .1u | C0402 | 1 |  |  |  |  | GRM155R62A104KE14D
C4 | 5185 | 1370 | 0 | 2 | 1 | 102.36 | 51.18 | 0.1u | C0805 | 1 |  |  |  |  | CL21B104KCFNNNE
C40 | 3410 | 4745 | 0 | 2 | 1 | 62.99 | 23.62 | 100p | C0402 | 1 |  |  |  |  | CC0402JRNPO9BN101
C41 | 3535 | 4470 | 90 | 2 | 1 | 62.99 | 23.62 | .1u | C0402 | 1 |  |  |  |  | GRM155R62A104KE14D
C42 | 3435 | 4420 | 270 | 2 | 1 | 62.99 | 23.62 | .1u | C0402 | 1 |  |  |  |  | GRM155R62A104KE14D
C43 | 4885 | 4745 | 0 | 2 | 1 | 62.99 | 23.62 | 100p | C0402 | 1 |  |  |  |  | CC0402JRNPO9BN101
C44 | 6485 | 4470 | 90 | 2 | 1 | 62.99 | 23.62 | .1u | C0402 | 1 |  |  |  |  | GRM155R62A104KE14D
C45 | 4910 | 4420 | 270 | 2 | 1 | 62.99 | 23.62 | .1u | C0402 | 1 |  |  |  |  | GRM155R62A104KE14D
C46 | 6360 | 4745 | 0 | 2 | 1 | 62.99 | 23.62 | 100p | C0402 | 1 |  |  |  |  | CC0402JRNPO9BN101
C47 | 5010 | 4470 | 90 | 2 | 1 | 62.99 | 23.62 | .1u | C0402 | 1 |  |  |  |  | GRM155R62A104KE14D
C48 | 6385 | 4420 | 270 | 2 | 1 | 62.99 | 23.62 | .1u | C0402 | 1 |  |  |  |  | GRM155R62A104KE14D
C49 | 6310 | 2820 | 180 | 2 | 1 | 62.99 | 23.62 | .1u | C0402 | 1 |  |  |  |  | GRM155R62A104KE14D
C5 | 3460 | 770 | 270 | 2 | 1 | 149.61 | 62.99 | 1u | C1206 | 1 |  |  |  |  | CL31B105KCHNNNE
C50 | 6260 | 2745 | 180 | 2 | 1 | 149.61 | 62.99 | 33u | CP1206 | 1 |  |  |  |  | TAJA336K010RNJ
C51 | 5390 | 4190 | 90 | 2 | 1 | 62.99 | 23.62 | .1u | C0402 | 1 |  |  |  |  | GRM155R62A104KE14D
C52 | 5385 | 2395 | 270 | 2 | 1 | 62.99 | 23.62 | 22p | C0402 | 1
C53 | 5385 | 2295 | 90 | 2 | 1 | 62.99 | 23.62 | 22p | C0402 | 1
C6 | 410 | 770 | 270 | 2 | 1 | 149.61 | 62.99 | 1u | C1206 | 1 |  |  |  |  | CL31B105KCHNNNE
C7 | 760 | 1370 | 0 | 2 | 1 | 102.36 | 51.18 | 0.1u | C0805 | 1 |  |  |  |  | CL21B104KCFNNNE
C8 | 2235 | 1370 | 0 | 2 | 1 | 102.36 | 51.18 | 0.1u | C0805 | 1 |  |  |  |  | CL21B104KCFNNNE
C9 | 4710 | 1045 | 0 | 2 | 1 | 149.61 | 62.99 | 1u | C1206 | 1 |  |  |  |  | CL31B105KCHNNNE
COMMUNICATION | 3610 | 4070 | 180 | 2 | 2 | 733.46 | 33.46 | 8x1F-H8.5 | 1X08 | 1 |  |  |  |  | 61300811121
CON1 | 4666.1 | 470 | 0 | 2 | 2 | 192.91 | 55.12 | CON23.5MM | PHOENIX_2_45 | 1 |  |  |  |  | 1988956
CON10 | 4847.8 | 4145 | 180 | 2 | 2 | 330.71 | 55.12 | CON3 | PHOENIX_3_45 | 1 |  |  |  |  | 1988969
CON11 | 7785 | 1245 | 90 | 2 | 2 | 459.06 | 459.06 | CON210.16MM | PHOENIX_2_10.16MM | 1 |  |  |  |  | 1773976
CON12 | 7328.11 | 3134.17 | 90 | 2 | 2 | 212.6 | 555.12 | CON1 | 1932575 | 1 |  |  |  |  | 1932575
CON13 | 7328.11 | 4409.17 | 90 | 2 | 2 | 212.6 | 555.12 | CON1 | 1932575 | 1 |  |  |  |  | 1932575
CON14 | 6253.9 | 4145 | 180 | 2 | 2 | 192.91 | 55.12 | CON23.5MM | PHOENIX_2_45 | 1 |  |  |  |  | 1988956
CON15 | 5633.23 | 2995 | 0 | 2 | 2 | 606.3 | 55.12 | CON5 | PHOENIX_5_45 | 1 |  |  |  |  | 1988985
CON2 | 6141.1 | 470 | 0 | 2 | 2 | 192.91 | 55.12 | CON23.5MM | PHOENIX_2_45 | 1 |  |  |  |  | 1988956
CON3 | 1716.1 | 470 | 0 | 2 | 2 | 192.91 | 55.12 | CON23.5MM | PHOENIX_2_45 | 1 |  |  |  |  | 1988956
CON4 | 3191.1 | 470 | 0 | 2 | 2 | 192.91 | 55.12 | CON23.5MM | PHOENIX_2_45 | 1 |  |  |  |  | 1988956
CON5 | 803.9 | 5720 | 180 | 2 | 2 | 192.91 | 55.12 | CON23.5MM | PHOENIX_2_45 | 1 |  |  |  |  | 1988956
CON6 | 2278.9 | 5720 | 180 | 2 | 2 | 192.91 | 55.12 | CON23.5MM | PHOENIX_2_45 | 1 |  |  |  |  | 1988956
CON7 | 3753.9 | 5720 | 180 | 2 | 2 | 192.91 | 55.12 | CON23.5MM | PHOENIX_2_45 | 1 |  |  |  |  | 1988956
CON8 | 5228.9 | 5720 | 180 | 2 | 2 | 192.91 | 55.12 | CON23.5MM | PHOENIX_2_45 | 1 |  |  |  |  | 1988956
CON9 | 4847.2 | 2995 | 0 | 2 | 2 | 330.71 | 55.12 | CON3 | PHOENIX_3_45 | 1 |  |  |  |  | 1988969
D1 | 4660 | 895 | 0 | 2 | 1 | 255.91 | 66.93 | DIODES_SMA | SMA | 1 |  |  |  |  | US1B-13-F
D10 | 735 | 1770 | 90 | 2 | 1 | 165.35 | 47.24 | DIODES_SOD-123 | SOD-123 | 1 |  |  |  |  | B0520LW-7-F
D11 | 2210 | 1770 | 90 | 2 | 1 | 165.35 | 47.24 | DIODES_SOD-123 | SOD-123 | 1 |  |  |  |  | B0520LW-7-F
D12 | 3685 | 1770 | 90 | 2 | 1 | 165.35 | 47.24 | DIODES_SOD-123 | SOD-123 | 1 |  |  |  |  | B0520LW-7-F
D13 | 6210 | 4420 | 270 | 2 | 1 | 165.35 | 47.24 | DIODES_SOD-123 | SOD-123 | 1 |  |  |  |  | B0520LW-7-F
D14 | 1785 | 4420 | 270 | 2 | 1 | 165.35 | 47.24 | DIODES_SOD-123 | SOD-123 | 1 |  |  |  |  | B0520LW-7-F
D15 | 3260 | 4420 | 270 | 2 | 1 | 165.35 | 47.24 | DIODES_SOD-123 | SOD-123 | 1 |  |  |  |  | B0520LW-7-F
D16 | 4735 | 4420 | 270 | 2 | 1 | 165.35 | 47.24 | DIODES_SOD-123 | SOD-123 | 1 |  |  |  |  | B0520LW-7-F
D17 | 5260 | 3680 | 90 | 2 | 1 | 90.55 | 31.5 |  | LED0603 | 1 |  |  |  |  | 150060BS75000
D18 | 6110 | 2680 | 270 | 2 | 1 | 90.55 | 31.5 |  | LED0603 | 1 |  |  |  |  | 150060BS75000
D19 | 5275 | 4120 | 0 | 2 | 1 | 90.55 | 31.5 |  | LED0603 | 1 |  |  |  |  | 150060BS75000
D2 | 6135 | 895 | 0 | 2 | 1 | 255.91 | 66.93 | DIODES_SMA | SMA | 1 |  |  |  |  | US1B-13-F
D20 | 5275 | 4270 | 0 | 2 | 1 | 90.55 | 31.5 |  | LED0603 | 1 |  |  |  |  | 150060BS75000
D21 | 4735 | 2370 | 0 | 2 | 1 | 90.55 | 31.5 |  | LED0603 | 1 |  |  |  |  | 150060BS75000
D3 | 1710 | 895 | 0 | 2 | 1 | 255.91 | 66.93 | DIODES_SMA | SMA | 1 |  |  |  |  | US1B-13-F
D4 | 3185 | 895 | 0 | 2 | 1 | 255.91 | 66.93 | DIODES_SMA | SMA | 1 |  |  |  |  | US1B-13-F
D5 | 810 | 5295 | 180 | 2 | 1 | 255.91 | 66.93 | DIODES_SMA | SMA | 1 |  |  |  |  | US1B-13-F
D6 | 2285 | 5295 | 180 | 2 | 1 | 255.91 | 66.93 | DIODES_SMA | SMA | 1 |  |  |  |  | US1B-13-F
D7 | 3760 | 5295 | 180 | 2 | 1 | 255.91 | 66.93 | DIODES_SMA | SMA | 1 |  |  |  |  | US1B-13-F
D8 | 5235 | 5295 | 180 | 2 | 1 | 255.91 | 66.93 | DIODES_SMA | SMA | 1 |  |  |  |  | US1B-13-F
D9 | 5160 | 1770 | 90 | 2 | 1 | 165.35 | 47.24 | DIODES_SOD-123 | SOD-123 | 1 |  |  |  |  | B0520LW-7-F
F1 | 6785 | 570 | 0 | 2 | 2 | 559.06 | 153.54 | 20A | FUSE_ATO | 1 |  |  |  |  | 178.6165.0001
F2 | 6910 | 5655 | 0 | 2 | 2 | 559.06 | 153.54 | 20A | FUSE_ATO | 1 |  |  |  |  | 178.6165.0001
F3 | 6785 | 2820 | 270 | 2 | 2 | 559.06 | 153.54 | 40A | FUSE_ATO | 1 |  |  |  |  | 178.6165.0001
H1 | 4210 | 1095 | 270 | 2 | 1 | 614.17 | 540.16 | HEATSINK-TO-263 | HEATSINK-TO-263 | 1 |  |  |  |  | 219-263B-TR
H2 | 5685 | 1095 | 270 | 2 | 1 | 614.17 | 540.16 | HEATSINK-TO-263 | HEATSINK-TO-263 | 1 |  |  |  |  | 219-263B-TR
H3 | 1260 | 1095 | 270 | 2 | 1 | 614.17 | 540.16 | HEATSINK-TO-263 | HEATSINK-TO-263 | 1 |  |  |  |  | 219-263B-TR
H4 | 2735 | 1095 | 270 | 2 | 1 | 614.17 | 540.16 | HEATSINK-TO-263 | HEATSINK-TO-263 | 1 |  |  |  |  | 219-263B-TR
H5 | 1260 | 5095 | 90 | 2 | 1 | 614.17 | 540.16 | HEATSINK-TO-263 | HEATSINK-TO-263 | 1 |  |  |  |  | 219-263B-TR
H6 | 2735 | 5095 | 90 | 2 | 1 | 614.17 | 540.16 | HEATSINK-TO-263 | HEATSINK-TO-263 | 1 |  |  |  |  | 219-263B-TR
H7 | 4210 | 5095 | 90 | 2 | 1 | 614.17 | 540.16 | HEATSINK-TO-263 | HEATSINK-TO-263 | 1 |  |  |  |  | 219-263B-TR
H8 | 5685 | 5095 | 90 | 2 | 1 | 614.17 | 540.16 | HEATSINK-TO-263 | HEATSINK-TO-263 | 1 |  |  |  |  | 219-263B-TR
JP1 | 1750 | 4070 | 0 | 2 | 2 | 933.46 | 33.46 | 10x1F-H8.5 | 1X10 | 1 |  |  |  |  | 61301011121
JP2 | 5945 | 4085 | 0 | 2 | 2 | 36 | 136 |  | JP1 | 1 |  |  |  |  | 77311-118-02LF
L1 | 4710 | 1320 | 90 | 2 | 1 | 352.36 | 137.8 | 2.2u | SRP7050 | 1 |  |  |  |  | SRP7050TA-2R2M
L2 | 6185 | 1320 | 90 | 2 | 1 | 352.36 | 137.8 | 2.2u | SRP7050 | 1 |  |  |  |  | SRP7050TA-2R2M
L3 | 1760 | 1320 | 90 | 2 | 1 | 352.36 | 137.8 | 2.2u | SRP7050 | 1 |  |  |  |  | SRP7050TA-2R2M
L4 | 3235 | 1320 | 90 | 2 | 1 | 352.36 | 137.8 | 2.2u | SRP7050 | 1 |  |  |  |  | SRP7050TA-2R2M
L5 | 760 | 4870 | 270 | 2 | 1 | 352.36 | 137.8 | 2.2u | SRP7050 | 1 |  |  |  |  | SRP7050TA-2R2M
L6 | 2235 | 4870 | 270 | 2 | 1 | 352.36 | 137.8 | 2.2u | SRP7050 | 1 |  |  |  |  | SRP7050TA-2R2M
L7 | 3710 | 4870 | 270 | 2 | 1 | 352.36 | 137.8 | 2.2u | SRP7050 | 1 |  |  |  |  | SRP7050TA-2R2M
L8 | 5185 | 4870 | 270 | 2 | 1 | 352.36 | 137.8 | 2.2u | SRP7050 | 1 |  |  |  |  | SRP7050TA-2R2M
POWER | 2010 | 2170 | 0 | 2 | 2 | 733.46 | 33.46 | 8x1F-H8.5 | 1X08 | 1 |  |  |  |  | 61300811121
PWML | 2710 | 4070 | 180 | 2 | 2 | 733.46 | 33.46 | 8x1F-H8.5 | 1X08 | 1 |  |  |  |  | 61300811121
Q1 | 3998.98 | 1095 | 270 | 2 | 1 | 267.72 | 653.54 | N-FET-TO263 | TO-263-3 | 1 |  |  |  |  | IPB090N06N3 G
Q10 | 5145 | 3849.33 | 180 | 2 | 1 | 57.48 | 66.93 | RE1C002UN | EMT3F | 1 |  |  |  |  | RE1C002UNTCL
Q2 | 5473.98 | 1095 | 270 | 2 | 1 | 267.72 | 653.54 | N-FET-TO263 | TO-263-3 | 1 |  |  |  |  | IPB090N06N3 G
Q3 | 1048.98 | 1095 | 270 | 2 | 1 | 267.72 | 653.54 | N-FET-TO263 | TO-263-3 | 1 |  |  |  |  | IPB090N06N3 G
Q4 | 2523.98 | 1095 | 270 | 2 | 1 | 267.72 | 653.54 | N-FET-TO263 | TO-263-3 | 1 |  |  |  |  | IPB090N06N3 G
Q5 | 1471.02 | 5095 | 90 | 2 | 1 | 267.72 | 653.54 | N-FET-TO263 | TO-263-3 | 1 |  |  |  |  | IPB090N06N3 G
Q6 | 2946.02 | 5095 | 90 | 2 | 1 | 267.72 | 653.54 | N-FET-TO263 | TO-263-3 | 1 |  |  |  |  | IPB090N06N3 G
Q7 | 4421.02 | 5095 | 90 | 2 | 1 | 267.72 | 653.54 | N-FET-TO263 | TO-263-3 | 1 |  |  |  |  | IPB090N06N3 G
Q8 | 5896.02 | 5095 | 90 | 2 | 1 | 267.72 | 653.54 | N-FET-TO263 | TO-263-3 | 1 |  |  |  |  | IPB090N06N3 G
Q9 | 6735 | 2195 | 180 | 2 | 1 | 114.17 | 106.3 |  | SOT-23-3 | 1 |  |  |  |  | SSM3K341R,LF
R1 | 710 | 995 | 0 | 2 | 1 | 62.99 | 23.62 | 10k | R0402 | 1
R10 | 4960 | 1195 | 180 | 2 | 1 | 102.36 | 51.18 | 0 | R0805 | 0 |  |  |  |  | MF-RES-0402-0
R100 | 4610 | 2370 | 0 | 2 | 1 | 62.99 | 23.62 | 1k | R0402 | 1
R101 | 6210 | 2820 | 0 | 2 | 1 | 62.99 | 23.62 | 0.3 | R0402 | 1 |  |  |  |  | ERJ-2BQFR30X
R102 | 5835 | 4140 | 90 | 2 | 1 | 62.99 | 23.62 | 120 | R0402 | 1 |  |  |  |  | ERJ-2RKF1200X
R103 | 5265 | 3550 | 90 | 2 | 1 | 62.99 | 23.62 | 1k | R0402 | 1
R104 | 4735 | 2645 | 90 | 2 | 1 | 62.99 | 23.62 | 10k | R0402 | 1
R105 | 5665 | 4040 | 90 | 2 | 1 | 62.99 | 23.62 | 47k | R0402 | 1 |  |  |  |  | ERJ-2RKF4702X
R106 | 5910 | 3420 | 90 | 2 | 1 | 62.99 | 23.62 | 0 | R0402 | 1
R107 | 5785 | 3420 | 90 | 2 | 1 | 62.99 | 23.62 | 0 | R0402 | 1
R108 | 5635 | 3420 | 90 | 2 | 1 | 62.99 | 23.62 | 0 | R0402 | 1
R109 | 5510 | 3420 | 90 | 2 | 1 | 62.99 | 23.62 | 0 | R0402 | 1
R11 | 685 | 1195 | 0 | 2 | 1 | 149.61 | 62.99 | 0.02 | R1206 | 1 |  |  |  |  | ERJ8CWFR020V
R110 | 5360 | 3420 | 90 | 2 | 1 | 62.99 | 23.62 | 0 | R0402 | 1
R111 | 5360 | 3520 | 270 | 2 | 1 | 62.99 | 23.62 | DNP | R0402 | 0
R112 | 5510 | 3520 | 270 | 2 | 1 | 62.99 | 23.62 | DNP | R0402 | 0
R113 | 5635 | 3520 | 270 | 2 | 1 | 62.99 | 23.62 | DNP | R0402 | 0
R114 | 5785 | 3520 | 270 | 2 | 1 | 62.99 | 23.62 | DNP | R0402 | 0
R115 | 5910 | 3520 | 270 | 2 | 1 | 62.99 | 23.62 | DNP | R0402 | 0
R12 | 2160 | 1195 | 0 | 2 | 1 | 149.61 | 62.99 | 0.02 | R1206 | 1 |  |  |  |  | ERJ8CWFR020V
R13 | 3660 | 995 | 0 | 2 | 1 | 62.99 | 23.62 | 10k | R0402 | 1
R14 | 5135 | 995 | 0 | 2 | 1 | 62.99 | 23.62 | 10k | R0402 | 1
R15 | 535 | 1195 | 180 | 2 | 1 | 102.36 | 51.18 | 0 | R0805 | 0 |  |  |  |  | MF-RES-0402-0
R16 | 2010 | 1195 | 180 | 2 | 1 | 102.36 | 51.18 | 0 | R0805 | 0 |  |  |  |  | MF-RES-0402-0
R17 | 1810 | 5195 | 180 | 2 | 1 | 62.99 | 23.62 | 10k | R0402 | 1
R18 | 3285 | 5195 | 180 | 2 | 1 | 62.99 | 23.62 | 10k | R0402 | 1
R19 | 4760 | 5195 | 180 | 2 | 1 | 62.99 | 23.62 | 10k | R0402 | 1
R2 | 2185 | 995 | 0 | 2 | 1 | 62.99 | 23.62 | 10k | R0402 | 1
R20 | 6235 | 5195 | 180 | 2 | 1 | 62.99 | 23.62 | 10k | R0402 | 1
R21 | 1610 | 4820 | 180 | 2 | 1 | 102.36 | 51.18 | 100 | R0805 | 1
R22 | 3085 | 4820 | 180 | 2 | 1 | 102.36 | 51.18 | 100 | R0805 | 1
R23 | 4560 | 4820 | 180 | 2 | 1 | 102.36 | 51.18 | 100 | R0805 | 1
R24 | 6035 | 4820 | 180 | 2 | 1 | 102.36 | 51.18 | 100 | R0805 | 1
R25 | 1835 | 4995 | 180 | 2 | 1 | 149.61 | 62.99 | 0.02 | R1206 | 1 |  |  |  |  | ERJ8CWFR020V
R26 | 3310 | 4995 | 180 | 2 | 1 | 149.61 | 62.99 | 0.02 | R1206 | 1 |  |  |  |  | ERJ8CWFR020V
R27 | 4785 | 4995 | 180 | 2 | 1 | 149.61 | 62.99 | 0.02 | R1206 | 1 |  |  |  |  | ERJ8CWFR020V
R28 | 6260 | 4995 | 180 | 2 | 1 | 149.61 | 62.99 | 0.02 | R1206 | 1 |  |  |  |  | ERJ8CWFR020V
R29 | 1985 | 4995 | 0 | 2 | 1 | 102.36 | 51.18 | 0 | R0805 | 0 |  |  |  |  | MF-RES-0402-0
R3 | 3860 | 1370 | 0 | 2 | 1 | 102.36 | 51.18 | 100 | R0805 | 1
R30 | 3460 | 4995 | 0 | 2 | 1 | 102.36 | 51.18 | 0 | R0805 | 0 |  |  |  |  | MF-RES-0402-0
R31 | 4935 | 4995 | 0 | 2 | 1 | 102.36 | 51.18 | 0 | R0805 | 0 |  |  |  |  | MF-RES-0402-0
R32 | 6410 | 4995 | 0 | 2 | 1 | 102.36 | 51.18 | 0 | R0805 | 0 |  |  |  |  | MF-RES-0402-0
R33 | 510 | 1770 | 270 | 2 | 1 | 62.99 | 23.62 | 100k | R0402 | 1
R34 | 1985 | 1770 | 270 | 2 | 1 | 62.99 | 23.62 | 100k | R0402 | 1
R35 | 3460 | 1770 | 270 | 2 | 1 | 62.99 | 23.62 | 100k | R0402 | 1
R36 | 560 | 1370 | 270 | 2 | 1 | 62.99 | 23.62 | 1k | R0402 | 1
R37 | 610 | 1370 | 270 | 2 | 1 | 62.99 | 23.62 | 1k | R0402 | 1
R38 | 2035 | 1370 | 270 | 2 | 1 | 62.99 | 23.62 | 1k | R0402 | 1
R39 | 2085 | 1370 | 270 | 2 | 1 | 62.99 | 23.62 | 1k | R0402 | 1
R4 | 5335 | 1370 | 0 | 2 | 1 | 102.36 | 51.18 | 100 | R0805 | 1
R40 | 3510 | 1370 | 270 | 2 | 1 | 62.99 | 23.62 | 1k | R0402 | 1
R41 | 3560 | 1370 | 270 | 2 | 1 | 62.99 | 23.62 | 1k | R0402 | 1
R42 | 635 | 1795 | 0 | 2 | 1 | 62.99 | 23.62 | 1k | R0402 | 1
R43 | 2110 | 1795 | 0 | 2 | 1 | 62.99 | 23.62 | 1k | R0402 | 1
R44 | 3585 | 1795 | 0 | 2 | 1 | 62.99 | 23.62 | 1k | R0402 | 1
R45 | 710 | 1620 | 90 | 2 | 1 | 62.99 | 23.62 | 100k | R0402 | 1
R46 | 2185 | 1620 | 90 | 2 | 1 | 62.99 | 23.62 | 100k | R0402 | 1
R47 | 3660 | 1620 | 90 | 2 | 1 | 62.99 | 23.62 | 100k | R0402 | 1
R48 | 635 | 1745 | 0 | 2 | 1 | 62.99 | 23.62 | 100k | R0402 | 1
R49 | 2110 | 1745 | 0 | 2 | 1 | 62.99 | 23.62 | 100k | R0402 | 1
R5 | 910 | 1370 | 0 | 2 | 1 | 102.36 | 51.18 | 100 | R0805 | 1
R50 | 3585 | 1745 | 0 | 2 | 1 | 62.99 | 23.62 | 100k | R0402 | 1
R51 | 560 | 1520 | 270 | 2 | 1 | 62.99 | 23.62 | 1k | R0402 | 1
R52 | 610 | 1520 | 270 | 2 | 1 | 62.99 | 23.62 | 1k | R0402 | 1
R53 | 2035 | 1520 | 270 | 2 | 1 | 62.99 | 23.62 | 1k | R0402 | 1
R54 | 2085 | 1520 | 270 | 2 | 1 | 62.99 | 23.62 | 1k | R0402 | 1
R55 | 3510 | 1520 | 270 | 2 | 1 | 62.99 | 23.62 | 1k | R0402 | 1
R56 | 3560 | 1520 | 270 | 2 | 1 | 62.99 | 23.62 | 1k | R0402 | 1
R57 | 4935 | 1770 | 270 | 2 | 1 | 62.99 | 23.62 | 100k | R0402 | 1
R58 | 4985 | 1370 | 270 | 2 | 1 | 62.99 | 23.62 | 1k | R0402 | 1
R59 | 5035 | 1370 | 270 | 2 | 1 | 62.99 | 23.62 | 1k | R0402 | 1
R6 | 2385 | 1370 | 0 | 2 | 1 | 102.36 | 51.18 | 100 | R0805 | 1
R60 | 5060 | 1795 | 0 | 2 | 1 | 62.99 | 23.62 | 1k | R0402 | 1
R61 | 5135 | 1620 | 90 | 2 | 1 | 62.99 | 23.62 | 100k | R0402 | 1
R62 | 5060 | 1745 | 0 | 2 | 1 | 62.99 | 23.62 | 100k | R0402 | 1
R63 | 4985 | 1520 | 270 | 2 | 1 | 62.99 | 23.62 | 1k | R0402 | 1
R64 | 5035 | 1520 | 270 | 2 | 1 | 62.99 | 23.62 | 1k | R0402 | 1
R65 | 2010 | 4420 | 90 | 2 | 1 | 62.99 | 23.62 | 100k | R0402 | 1
R66 | 3485 | 4420 | 90 | 2 | 1 | 62.99 | 23.62 | 100k | R0402 | 1
R67 | 4960 | 4420 | 90 | 2 | 1 | 62.99 | 23.62 | 100k | R0402 | 1
R68 | 1960 | 4820 | 90 | 2 | 1 | 62.99 | 23.62 | 1k | R0402 | 1
R69 | 1910 | 4820 | 90 | 2 | 1 | 62.99 | 23.62 | 1k | R0402 | 1
R7 | 3635 | 1195 | 0 | 2 | 1 | 149.61 | 62.99 | 0.02 | R1206 | 1 |  |  |  |  | ERJ8CWFR020V
R70 | 3435 | 4820 | 90 | 2 | 1 | 62.99 | 23.62 | 1k | R0402 | 1
R71 | 3385 | 4820 | 90 | 2 | 1 | 62.99 | 23.62 | 1k | R0402 | 1
R72 | 4910 | 4820 | 90 | 2 | 1 | 62.99 | 23.62 | 1k | R0402 | 1
R73 | 4860 | 4820 | 90 | 2 | 1 | 62.99 | 23.62 | 1k | R0402 | 1
R74 | 1885 | 4395 | 180 | 2 | 1 | 62.99 | 23.62 | 1k | R0402 | 1
R75 | 3360 | 4395 | 180 | 2 | 1 | 62.99 | 23.62 | 1k | R0402 | 1
R76 | 4835 | 4395 | 180 | 2 | 1 | 62.99 | 23.62 | 1k | R0402 | 1
R77 | 1810 | 4570 | 270 | 2 | 1 | 62.99 | 23.62 | 100k | R0402 | 1
R78 | 3285 | 4570 | 270 | 2 | 1 | 62.99 | 23.62 | 100k | R0402 | 1
R79 | 4760 | 4570 | 270 | 2 | 1 | 62.99 | 23.62 | 100k | R0402 | 1
R8 | 5110 | 1195 | 0 | 2 | 1 | 149.61 | 62.99 | 0.02 | R1206 | 1 |  |  |  |  | ERJ8CWFR020V
R80 | 1885 | 4445 | 180 | 2 | 1 | 62.99 | 23.62 | 100k | R0402 | 1
R81 | 3360 | 4445 | 180 | 2 | 1 | 62.99 | 23.62 | 100k | R0402 | 1
R82 | 4835 | 4445 | 180 | 2 | 1 | 62.99 | 23.62 | 100k | R0402 | 1
R83 | 1960 | 4670 | 90 | 2 | 1 | 62.99 | 23.62 | 1k | R0402 | 1
R84 | 1910 | 4670 | 90 | 2 | 1 | 62.99 | 23.62 | 1k | R0402 | 1
R85 | 3435 | 4670 | 90 | 2 | 1 | 62.99 | 23.62 | 1k | R0402 | 1
R86 | 3385 | 4670 | 90 | 2 | 1 | 62.99 | 23.62 | 1k | R0402 | 1
R87 | 4910 | 4670 | 90 | 2 | 1 | 62.99 | 23.62 | 1k | R0402 | 1
R88 | 4860 | 4670 | 90 | 2 | 1 | 62.99 | 23.62 | 1k | R0402 | 1
R89 | 6435 | 4420 | 90 | 2 | 1 | 62.99 | 23.62 | 100k | R0402 | 1
R9 | 3485 | 1195 | 180 | 2 | 1 | 102.36 | 51.18 | 0 | R0805 | 0 |  |  |  |  | MF-RES-0402-0
R90 | 6385 | 4820 | 90 | 2 | 1 | 62.99 | 23.62 | 1k | R0402 | 1
R91 | 6335 | 4820 | 90 | 2 | 1 | 62.99 | 23.62 | 1k | R0402 | 1
R92 | 6310 | 4395 | 180 | 2 | 1 | 62.99 | 23.62 | 1k | R0402 | 1
R93 | 6235 | 4570 | 270 | 2 | 1 | 62.99 | 23.62 | 100k | R0402 | 1
R94 | 6310 | 4445 | 180 | 2 | 1 | 62.99 | 23.62 | 100k | R0402 | 1
R95 | 6385 | 4670 | 90 | 2 | 1 | 62.99 | 23.62 | 1k | R0402 | 1
R96 | 6335 | 4670 | 90 | 2 | 1 | 62.99 | 23.62 | 1k | R0402 | 1
R97 | 6120 | 2795 | 270 | 2 | 1 | 62.99 | 23.62 | 1k | R0402 | 1
R98 | 5160 | 4115 | 0 | 2 | 1 | 62.99 | 23.62 | 1k | R0402 | 1
R99 | 5155 | 4270 | 0 | 2 | 1 | 62.99 | 23.62 | 1k | R0402 | 1
RELAY1 | 4938.94 | 3570 | 0 | 2 | 1 | 443.31 | 405.12 | RELAY_DPDT | KEMET_EE2 | 1 |  |  |  |  | EE2-5NU-L
RELAY2 | 7485 | 2245 | 180 | 2 | 1 | 0 | 0 | RELAY_BOM | VCF4_RELAY | 1 |  |  |  |  | 1432868-1
RELAY3 | 7460 | 2222.36 | 270 | 2 | 2 | 795.28 | 755.91 | RELAY_VF4 | VCF4-SOCKET | 1 |  |  |  |  | VCF4-1000
TP1 | 1365 | 2115 | 0 | 2 | 1 | 45 | 45 |  | TP_4545 | 0
TP2 | 6525 | 950 | 0 | 2 | 1 | 45 | 45 |  | TP_4545 | 0
TP3 | 545 | 3890 | 0 | 2 | 1 | 45 | 45 |  | TP_4545 | 0
U1 | 760 | 620 | 90 | 2 | 1 | 173.62 | 267.72 | UCC27524 | SOIC-8 | 1 |  |  |  |  | UCC27524DR
U10 | 1935 | 4545 | 180 | 2 | 1 | 147.64 | 98.43 | OPA170 | SOT-23-5 | 1 |  |  |  |  | OPA170AIDBVT
U11 | 3410 | 4545 | 180 | 2 | 1 | 147.64 | 98.43 | OPA170 | SOT-23-5 | 1 |  |  |  |  | OPA170AIDBVT
U12 | 4885 | 4545 | 180 | 2 | 1 | 147.64 | 98.43 | OPA170 | SOT-23-5 | 1 |  |  |  |  | OPA170AIDBVT
U13 | 6335 | 3204.84 | 0 | 2 | 1 | 421.26 | 653.54 | TL750M | TO-263 | 1 |  |  |  |  | TL750M05CKVURG3
U14 | 5560 | 4195 | 270 | 2 | 1 | 173.62 | 267.72 | MCP2551 | SOIC8-6.0 | 1 |  |  |  |  | MCP2551-I/SN
U15 | 5060 | 2470 | 90 | 2 | 1 | 430 | 457 | MCP2515 | SOIC18 | 1 |  |  |  |  | MCP2515-I/SO
U2 | 3735 | 620 | 90 | 2 | 1 | 173.62 | 267.72 | UCC27524 | SOIC-8 | 1 |  |  |  |  | UCC27524DR
U3 | 3205 | 5570 | 270 | 2 | 1 | 173.62 | 267.72 | UCC27524 | SOIC-8 | 1 |  |  |  |  | UCC27524DR
U4 | 6160 | 5570 | 270 | 2 | 1 | 173.62 | 267.72 | UCC27524 | SOIC-8 | 1 |  |  |  |  | UCC27524DR
U5 | 5010 | 1645 | 0 | 2 | 1 | 147.64 | 98.43 | OPA170 | SOT-23-5 | 1 |  |  |  |  | OPA170AIDBVT
U6 | 585 | 1645 | 0 | 2 | 1 | 147.64 | 98.43 | OPA170 | SOT-23-5 | 1 |  |  |  |  | OPA170AIDBVT
U7 | 2060 | 1645 | 0 | 2 | 1 | 147.64 | 98.43 | OPA170 | SOT-23-5 | 1 |  |  |  |  | OPA170AIDBVT
U8 | 3535 | 1645 | 0 | 2 | 1 | 147.64 | 98.43 | OPA170 | SOT-23-5 | 1 |  |  |  |  | OPA170AIDBVT
U9 | 6360 | 4545 | 180 | 2 | 1 | 147.64 | 98.43 | OPA170 | SOT-23-5 | 1 |  |  |  |  | OPA170AIDBVT
X1 | 5535 | 2345 | 270 | 2 | 1 | 590 | 76 | 16MHz | HC49UP | 1 |  |  |  |  | ABLS-16.000MHZ-D-4-T
XIO | 4310 | 3220 | 270 | 2 | 2 | 1737.4 | 137.4 | 18x2F-H8.5 | 2X18 | 1 |  |  |  |  | 61303621121

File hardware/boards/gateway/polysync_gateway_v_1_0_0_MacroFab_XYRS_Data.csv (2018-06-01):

# Generated by MacroFab for PCB 7n6gav, version 1.
# DESIGNATOR | X_LOC | Y_LOC | ROTATION | SIDE | TYPE | X_SIZE | Y_SIZE | VALUE | FOOTPRINT | POPULATE | MPN | MPN1 | MPN2 | MPN3
C1 | 780 | 1555 | 90 | 1 | 1 | 62.99 | 23.62 | .1u | C0402 | 1
C2 | 1040 | 1225 | 0 | 1 | 1 | 62.99 | 23.62 | .1u | C0402 | 1
C3 | 680 | 1530 | 90 | 1 | 1 | 149.61 | 62.99 | 33u | CP1206 | 1 |  |  |  |  | TAJA336K010RNJ
C4 | 1005 | 405 | 270 | 1 | 1 | 62.99 | 23.62 | 22p | C0402 | 1
C5 | 1065 | 1295 | 0 | 1 | 1 | 102.36 | 51.18 | 10u | C0805 | 1 |  |  |  |  | LMK212B7106KG-TD
C6 | 745 | 850 | 270 | 1 | 1 | 62.99 | 23.62 | .1u | C0402 | 1
C7 | 1005 | 505 | 90 | 1 | 1 | 62.99 | 23.62 | 22p | C0402 | 1
CON1 | 180 | 1686.1 | 270 | 1 | 2 | 192.91 | 55.12 | CON2 | PHOENIX_2_45 | 1 |  |  |  |  | 1988956
CON2 | 180 | 536.1 | 270 | 1 | 2 | 192.91 | 55.12 | CON2 | PHOENIX_2_45 | 1 |  |  |  |  | 1988956
CON3 | 2380 | 636.69 | 90 | 1 | 2 | 468.5 | 55.12 | CON4 | PHOENIX_4_45 | 1 |  |  |  |  | 1988972
CON4 | 2380 | 1586.69 | 90 | 1 | 2 | 468.5 | 55.12 | CON4 | PHOENIX_4_45 | 1 |  |  |  |  | 1988972
D1 | 2205 | 1180 | 270 | 1 | 1 | 90.55 | 31.5 |  | LED0603 | 1 |  |  |  |  | 150060BS75000
D2 | 230 | 330 | 180 | 1 | 1 | 90.55 | 31.5 |  | LED0603 | 1 |  |  |  |  | 150060BS75000
D3 | 230 | 255 | 180 | 1 | 1 | 90.55 | 31.5 |  | LED0603 | 1 |  |  |  |  | 150060BS75000
D4 | 230 | 180 | 180 | 1 | 1 | 90.55 | 31.5 |  | LED0603 | 1 |  |  |  |  | 150060BS75000
D5 | 230 | 105 | 180 | 1 | 1 | 90.55 | 31.5 |  | LED0603 | 1 |  |  |  |  | 150060BS75000
JP1 | 1195 | 2005 | 0 | 2 | 2 | 935 | 35 | ARDUINO_JP1 | ARDUINO_JP1 | 1 |  |  |  |  | 68002-210HLF
JP2 | 2155 | 2005 | 0 | 2 | 2 | 735 | 35 | ARDUINO_JP2 | ARDUINO_JP2 | 1 |  |  |  |  | 68000-208HLF
JP3 | 2555 | 1105 | 0 | 2 | 2 | 135 | 235 | ARDUINO_JP3 | ARDUINO_JP3 | 1 |  |  |  |  | 68683-303LF
JP4 | 2255 | 105 | 0 | 2 | 2 | 535 | 35 | ARDUINO_JP4 | ARDUINO_JP4 | 1 |  |  |  |  | 68000-206HLF
JP5 | 1455 | 105 | 0 | 2 | 2 | 735 | 35 | ARDUINO_JP5 | ARDUINO_JP5 | 1 |  |  |  |  | 68000-208HLF
JP6 | 180 | 855 | 270 | 1 | 2 | 36 | 136 |  | JP1 | 1 |  |  |  |  | 77311-118-02LF
Q1 | 1660 | 1389.33 | 180 | 1 | 1 | 57.48 | 66.93 | RE1C002UN | EMT3F | 1 |  |  |  |  | RE1C002UNTCL
R1 | 2205 | 1030 | 270 | 1 | 1 | 62.99 | 23.62 | 1k | R0402 | 1
R10 | 1380 | 1140 | 180 | 1 | 1 | 62.99 | 23.62 | DNP | R0402 | 0
R11 | 1410 | 980 | 90 | 1 | 1 | 62.99 | 23.62 | 10k | R0402 | 1
R12 | 1360 | 980 | 270 | 1 | 1 | 62.99 | 23.62 | DNP | R0402 | 0
R13 | 380 | 855 | 180 | 1 | 1 | 62.99 | 23.62 | 120 | R0402 | 1 |  |  |  |  | ERJ-2RKF1200X
R14 | 380 | 780 | 180 | 1 | 1 | 62.99 | 23.62 | 47k | R0402 | 1 |  |  |  |  | ERJ-2RKF4702X
R15 | 1830 | 505 | 270 | 1 | 1 | 62.99 | 23.62 | 0 | R0402 | 1
R16 | 1880 | 505 | 270 | 1 | 1 | 62.99 | 23.62 | 0 | R0402 | 1
R17 | 1830 | 355 | 270 | 1 | 1 | 62.99 | 23.62 | DNP | R0402 | 0
R18 | 1880 | 355 | 270 | 1 | 1 | 62.99 | 23.62 | DNP | R0402 | 0
R19 | 1935 | 505 | 270 | 1 | 1 | 62.99 | 23.62 | 0 | R0402 | 1
R2 | 1725 | 755 | 270 | 1 | 1 | 62.99 | 23.62 | 10k | R0402 | 1
R20 | 1985 | 505 | 270 | 1 | 1 | 62.99 | 23.62 | 0 | R0402 | 1
R21 | 1935 | 355 | 270 | 1 | 1 | 62.99 | 23.62 | DNP | R0402 | 0
R22 | 1985 | 355 | 270 | 1 | 1 | 62.99 | 23.62 | DNP | R0402 | 0
R3 | 1380 | 1190 | 180 | 1 | 1 | 62.99 | 23.62 | 0 | R0402 | 1
R4 | 105 | 330 | 180 | 1 | 1 | 62.99 | 23.62 | 1k | R0402 | 1
R5 | 105 | 255 | 180 | 1 | 1 | 62.99 | 23.62 | 1k | R0402 | 1
R6 | 105 | 180 | 180 | 1 | 1 | 62.99 | 23.62 | 1k | R0402 | 1
R7 | 105 | 105 | 180 | 1 | 1 | 62.99 | 23.62 | 1k | R0402 | 1
R8 | 780 | 1455 | 270 | 1 | 1 | 62.99 | 23.62 | 0.3 | R0402 | 1 |  |  |  |  | ERJ-2BQFR30X
R9 | 1310 | 980 | 270 | 1 | 1 | 62.99 | 23.62 | 10k | R0402 | 1
RELAY1 | 1781.06 | 1115 | 0 | 1 | 1 | 443.31 | 405.12 | RELAY_DPDT | KEMET_EE2 | 1 |  |  |  |  | EE2-5NU-L
TP1 | 640 | 320 | 0 | 1 | 1 | 45 | 45 |  | TP_4545 | 0
TP2 | 2355 | 1090 | 0 | 1 | 1 | 45 | 45 |  | TP_4545 | 0
TP3 | 75 | 2040 | 0 | 1 | 1 | 45 | 45 |  | TP_4545 | 0
U$1 | 2295 | 1365 | 0 | 2 | 1 | 0 | 0 | POLYSYNC | POLYSYNC | 0
U1 | 575 | 845 | 90 | 1 | 1 | 173.62 | 267.72 | MCP2551 | SOIC8-6.0 | 1 |  |  |  |  | MCP2551-I/SN
U2 | 1455 | 580 | 270 | 1 | 1 | 430 | 457 | MCP2515 | SOIC18 | 1 |  |  |  |  | MCP2515-I/SO
U4 | 1144.84 | 1590 | 270 | 1 | 1 | 421.26 | 653.54 | TL750M | TO-263 | 1 |  |  |  |  | TL750M05CKTTR
U5 | 1125 | 1085 | 0 | 1 | 1 | 289.37 | 171.26 | MCP4922T | TSSOP-14 | 1 |  |  |  |  | MCP4922T-E/ST
X1 | 870 | 340 | 90 | 1 | 1 | 590 | 76 | 16MHz | HC49UP | 1 |  |  |  |  | ABLS-16.000MHZ-D-4-T

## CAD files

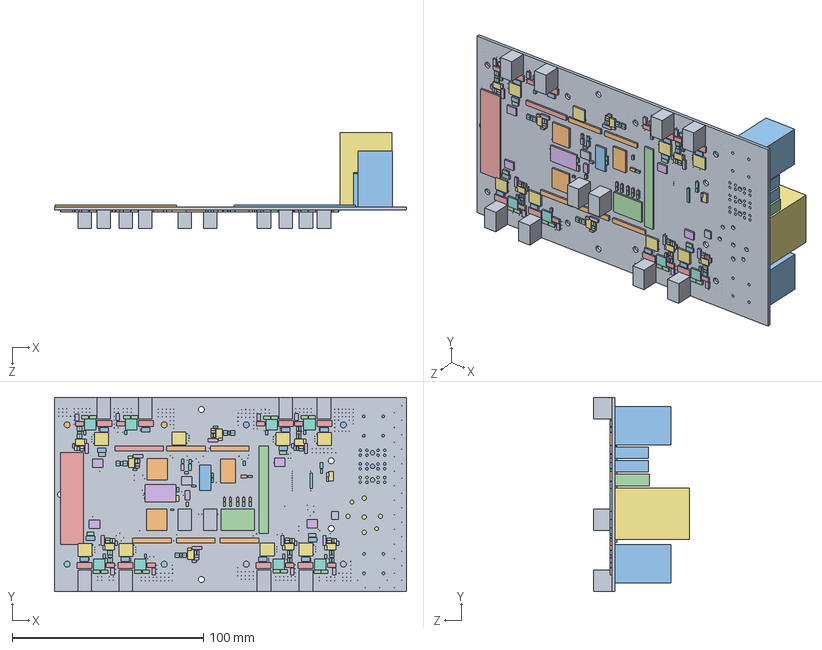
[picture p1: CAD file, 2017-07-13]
hardware/3d_models/brake_enclosure/actuator_control_board_1.0.0.SLDASM
184.1 x 101.6 x 50.0 mm
actuator_control_board_100
1X08_1X08 x 5
C1206_1U x 12
C0805_0_1U x 12
C0402_100P x 8
C0402__1U x 18
CP1206_33U
C0402_22P x 2
PHOENIX_2_45_CON23_5MM x 10
PHOENIX_3_45_CON3 x 2
PHOENIX_2_10_16MM_CON210_16MM x 2
PHOENIX_5_45_CON5
SMA_DIODES_SMA x 8
SOD123_DIODES_SOD123 x 8
LED0603_D17_LED0603
LED0603_GREEN x 2
LED0603_RED
LED0603_BLUE
FUSE_ATO_20A x 2
FUSE_ATO_40A
1X10_1X10
JP1_JP2_JP1
SRP7050_2_2U x 8
SON8DQJ_NFETTO263NEXFET x 8
SOT233_Q9_SOT233
EMT3F_RE1C002UN
R0402_10K x 9
R0805_100 x 8
R1206__02 x 8
R0805_0 x 8
R0402_100K x 24
R0402_1K x 45
R0402__3
R0402_120
R0402_47K
R0402_0 x 5
R0402_DNP x 5
KEMET_EE2_RELAY_DPDT
VCF4_RELAY_RELAY_BOM
HEATSINK_2X_75_U_3_HEATSINK_2X_75
HEATSINK_2X_75_U_7_HEATSINK_2X_75
HEATSINK_2X_75_U_9_HEATSINK_2X_75
HEATSINK_2X_75_U_10_HEATSINK_2X_75
OSCC_LOGO_U_11_OSCC_LOGO
POLYSYNC_U_13_POLYSYNC
SOIC8_UCC27524 x 4
SOT235_OPA170 x 8
TO263_TL750M
SOIC86_0_MCP2551
SOIC18_MCP2515
HC49UP_16MHZ
2X18_2X18

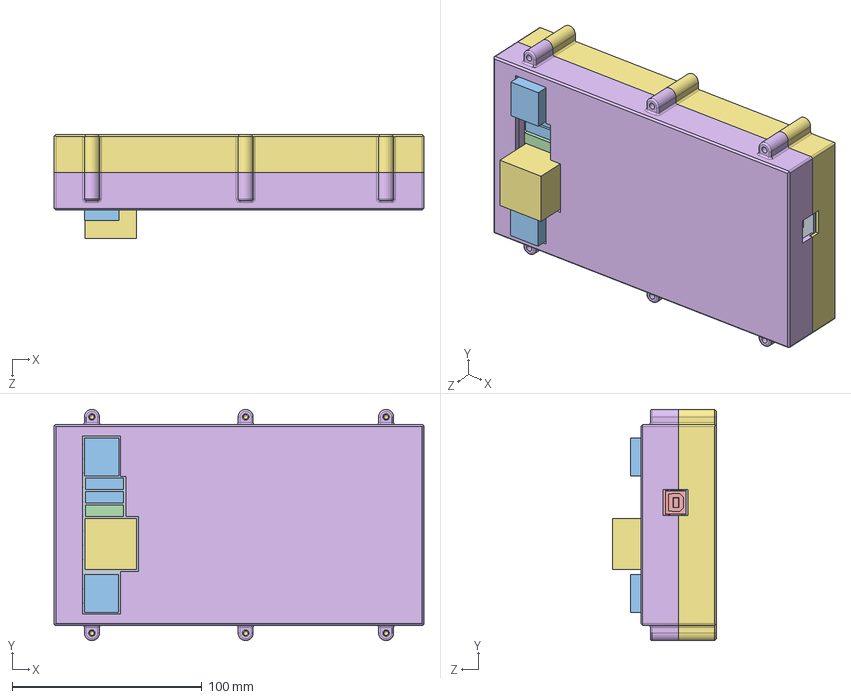
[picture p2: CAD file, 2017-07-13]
hardware/3d_models/brake_enclosure/actuator_control_board_enclosure_assembly.SLDASM
195.2 x 122.0 x 55.0 mm
actuator_control_board_100
1X08_1X08 x 5
C1206_1U x 12
C0805_0_1U x 12
C0402_100P x 8
C0402__1U x 18
CP1206_33U
C0402_22P x 2
PHOENIX_2_45_CON23_5MM x 10
PHOENIX_3_45_CON3 x 2
PHOENIX_2_10_16MM_CON210_16MM x 2
PHOENIX_5_45_CON5
SMA_DIODES_SMA x 8
SOD123_DIODES_SOD123 x 8
LED0603_D17_LED0603
LED0603_GREEN x 2
LED0603_RED
LED0603_BLUE
FUSE_ATO_20A x 2
FUSE_ATO_40A
1X10_1X10
JP1_JP2_JP1
SRP7050_2_2U x 8
SON8DQJ_NFETTO263NEXFET x 8
SOT233_Q9_SOT233
EMT3F_RE1C002UN
R0402_10K x 9
R0805_100 x 8
R1206__02 x 8
R0805_0 x 8
R0402_100K x 24
R0402_1K x 45
R0402__3
R0402_120
R0402_47K
R0402_0 x 5
R0402_DNP x 5
KEMET_EE2_RELAY_DPDT
VCF4_RELAY_RELAY_BOM
HEATSINK_2X_75_U_3_HEATSINK_2X_75
HEATSINK_2X_75_U_7_HEATSINK_2X_75
HEATSINK_2X_75_U_9_HEATSINK_2X_75
HEATSINK_2X_75_U_10_HEATSINK_2X_75
OSCC_LOGO_U_11_OSCC_LOGO
POLYSYNC_U_13_POLYSYNC
SOIC8_UCC27524 x 4
SOT235_OPA170 x 8
TO263_TL750M
SOIC86_0_MCP2551
SOIC18_MCP2515
HC49UP_16MHZ
2X18_2X18
ArduinoMega
actuator_control_board_enclosure_top
actuator_control_board_enclosure_bottom

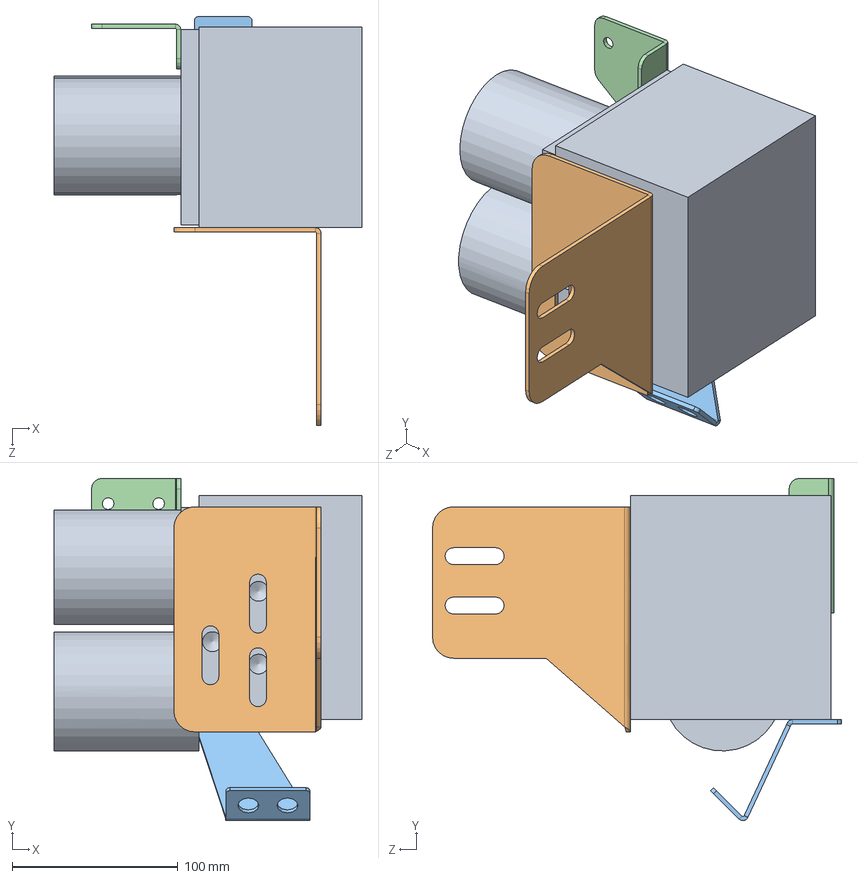
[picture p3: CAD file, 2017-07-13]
hardware/3d_models/kia_soul/actuator_bracket_assembly.SLDASM
185.7 x 206.6 x 246.8 mm
actuator_mockup
side_bracket
bottom_bracket
reservoir_bracket

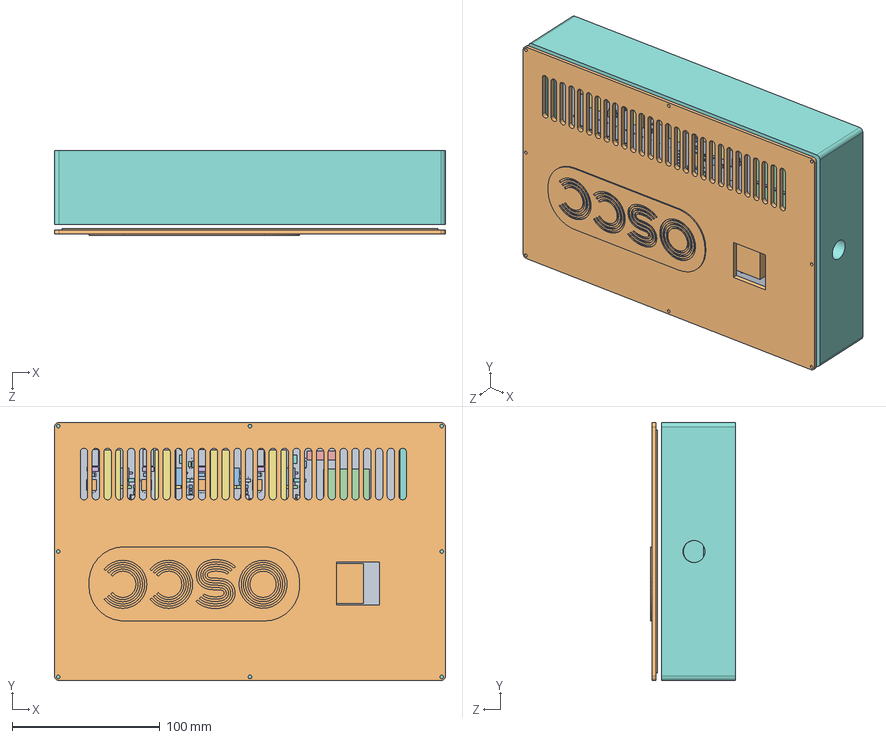
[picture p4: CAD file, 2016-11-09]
hardware/3d_models/brake_enclosure/brake_assembly.SLDASM
265.0 x 175.0 x 57.4 mm
polysync_braking
1X08_1X08 x 5
C1206_1U x 12
C0805_0_1U x 12
C0402_100P x 8
C0402__1U x 18
CP1206_33U
C0402_22P x 2
PHOENIX_2_45_CON23_5MM x 9
PHOENIX_3_45_CON3 x 2
PHOENIX_2_10_16MM_CON210_16MM
1932575_CON1 x 2
PHOENIX_5_45_CON5
SMA_DIODES_SMA x 8
SOD123_DIODES_SOD123 x 8
LED0603_D17_LED0603
LED0603_D18_LED0603
LED0603_D19_LED0603
LED0603_D20_LED0603
LED0603_D21_LED0603
FUSE_ATO_20A x 2
FUSE_ATO_40A
HEATSINKTO263_HEATSINKTO263 x 8
1X10_1X10
JP1_JP2_JP1
SRP7050_2_2U x 8
TO2633_NFETTO263 x 8
SOT233_Q9_SOT233
EMT3F_RE1C002UN
R0402_10K x 9
R0805_100 x 8
R1206__02 x 8
R0805_0 x 8
R0402_100K x 24
R0402_1K x 45
R0402__3
R0402_120
R0402_47K
R0402_0 x 5
R0402_DNP x 5
KEMET_EE2_RELAY_DPDT
VCF4_RELAY_RELAY_BOM
VCF4SOCKET_RELAY_VF4
TP_4545_TP1_TP_4545
TP_4545_TP2_TP_4545
TP_4545_TP3_TP_4545
POLYSYNC_BRAKE_TOP_U_8_POLYSYNC_BRAKE_TOP
SOIC8_UCC27524 x 4
SOT235_OPA170 x 8
TO263_TL750M
SOIC86_0_MCP2551
SOIC18_MCP2515
HC49UP_16MHZ
2X18_2X18
ArduinoMega
brake_housing
brake_cable_clamp
brake_house_lid

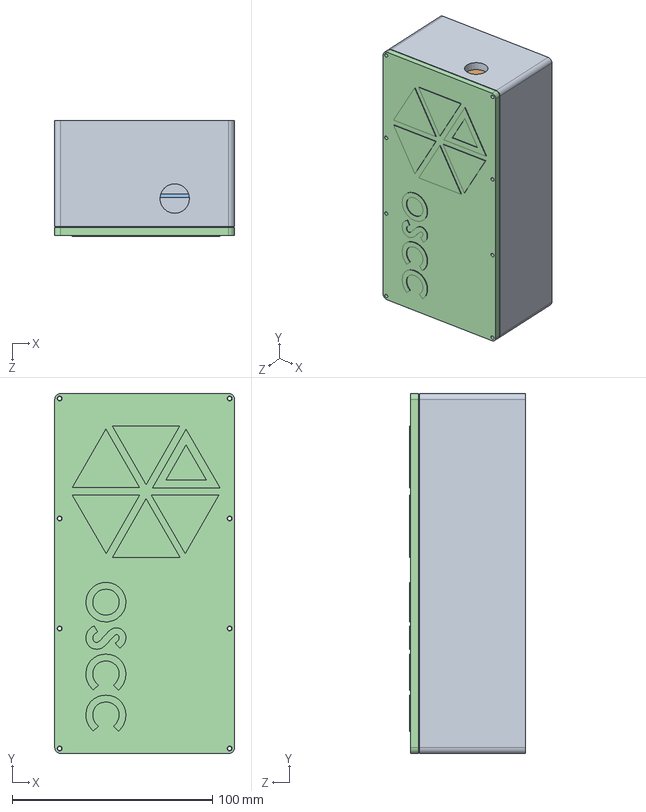
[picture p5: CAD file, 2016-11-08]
hardware/3d_models/dash_enclosure/STC_assembly.SLDASM
90.2 x 180.0 x 57.9 mm
STC_housing
ArduinoUnoMockup x 3
CANShieldMockup x 2
STC_lid

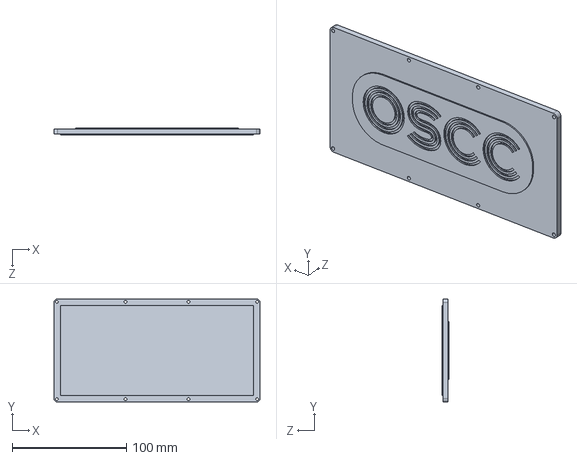
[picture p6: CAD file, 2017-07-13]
hardware/3d_models/dash_enclosure/STC_lid.SLDPRT
180.0 x 90.0 x 6.00 mm

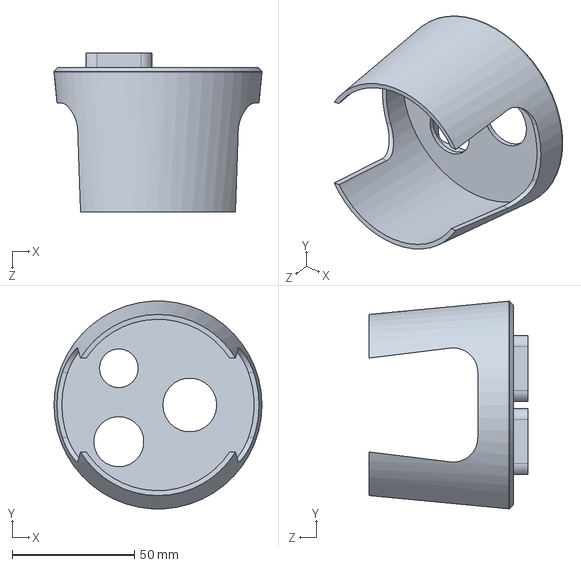
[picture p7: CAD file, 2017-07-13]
hardware/3d_models/estop_cupholder/EStopHousing.SLDPRT
85.0 x 84.8 x 65.0 mm

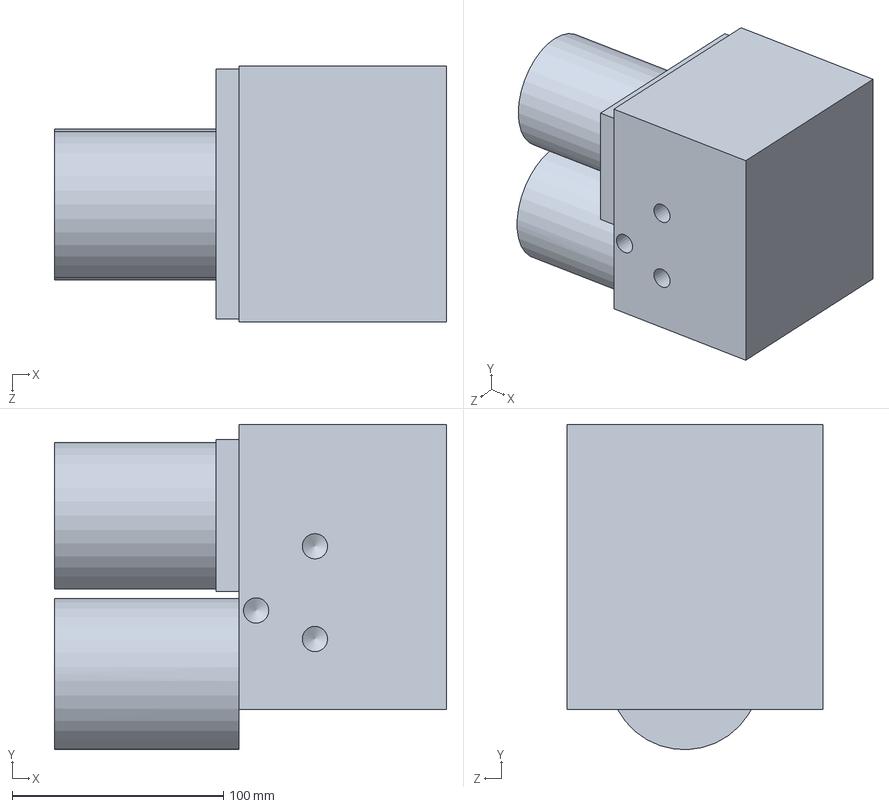
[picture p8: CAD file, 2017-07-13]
hardware/3d_models/kia_soul/actuator_mockup.SLDPRT
185.7 x 154.1 x 121.2 mm

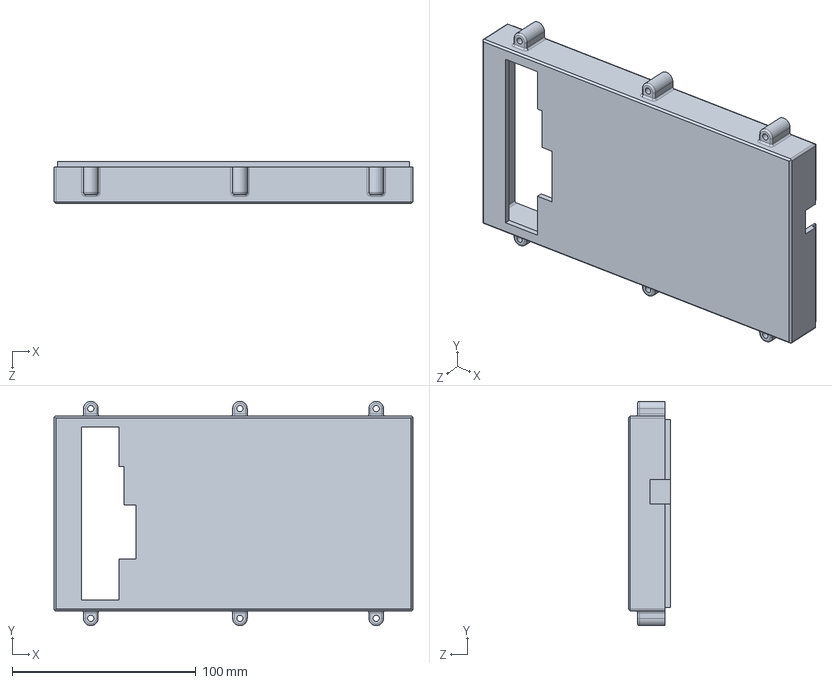
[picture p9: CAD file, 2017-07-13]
hardware/3d_models/brake_enclosure/actuator_control_board_enclosure_top.SLDPRT
195.2 x 122.0 x 23.0 mm

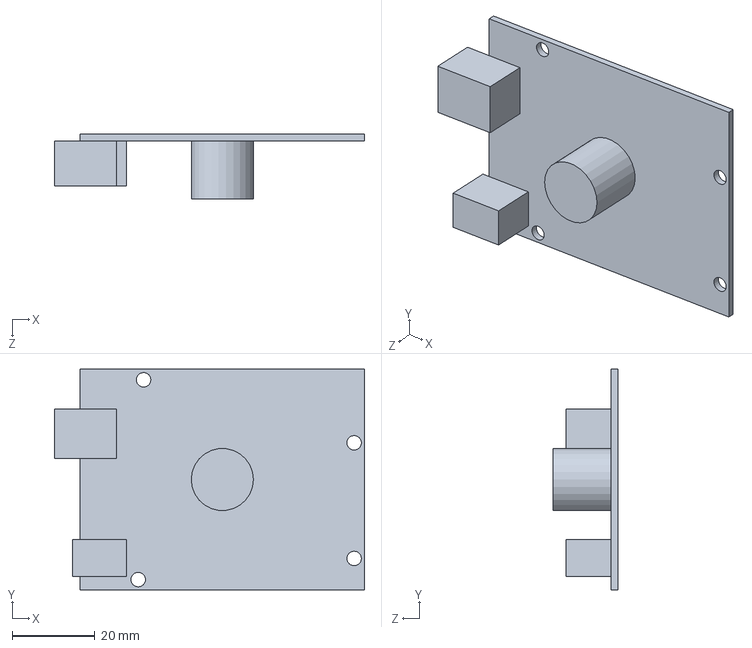
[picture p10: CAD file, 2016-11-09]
hardware/3d_models/dash_enclosure/ArduinoUnoMockup.SLDPRT
74.8 x 53.3 x 15.6 mm

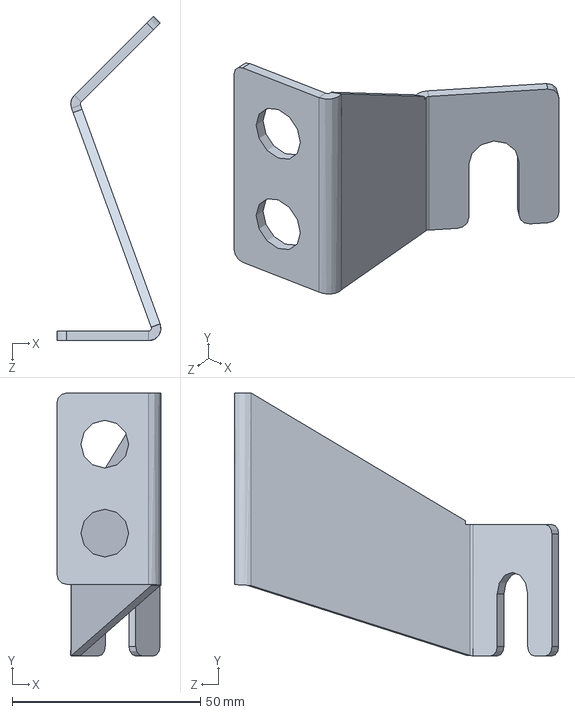
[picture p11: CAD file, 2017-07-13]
hardware/3d_models/kia_soul/bottom_bracket.SLDPRT
27.6 x 69.8 x 86.2 mm

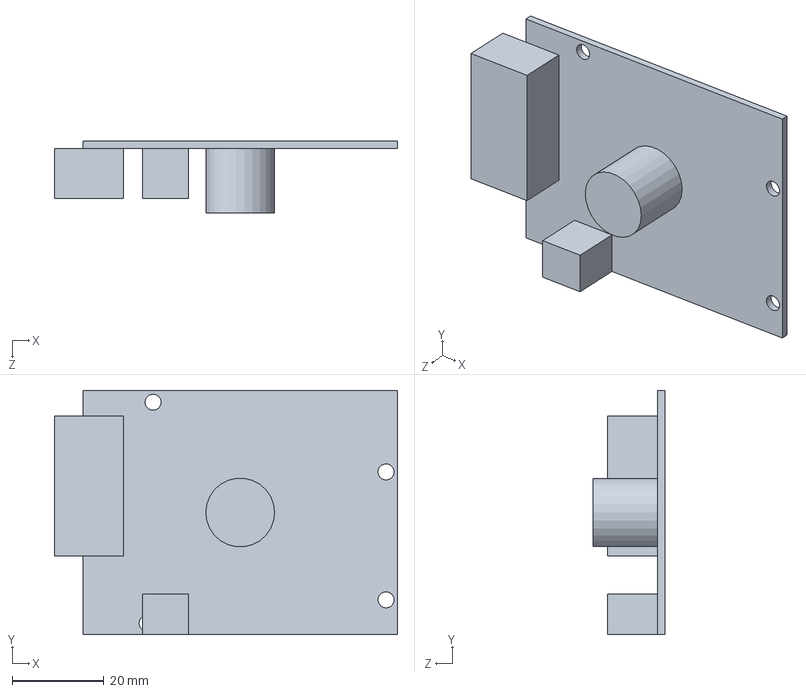
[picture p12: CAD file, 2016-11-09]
hardware/3d_models/dash_enclosure/CANShieldMockup.SLDPRT
74.8 x 53.3 x 15.6 mm

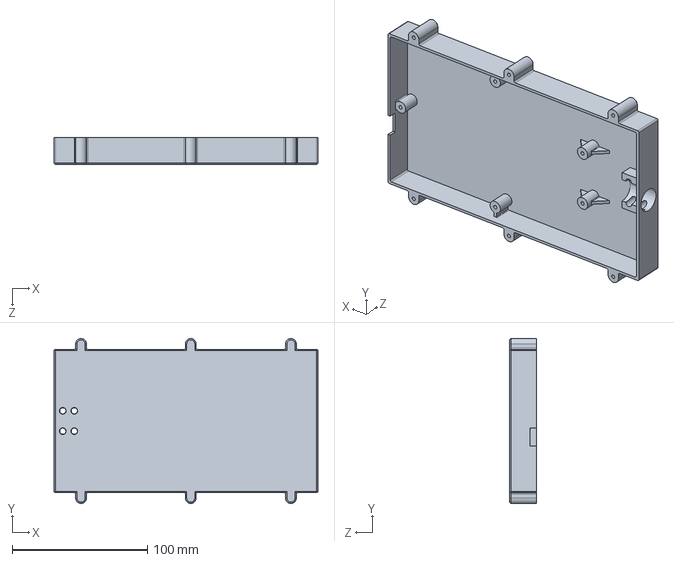
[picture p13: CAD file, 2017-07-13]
hardware/3d_models/brake_enclosure/actuator_control_board_enclosure_bottom.SLDPRT
195.2 x 122.0 x 20.0 mm

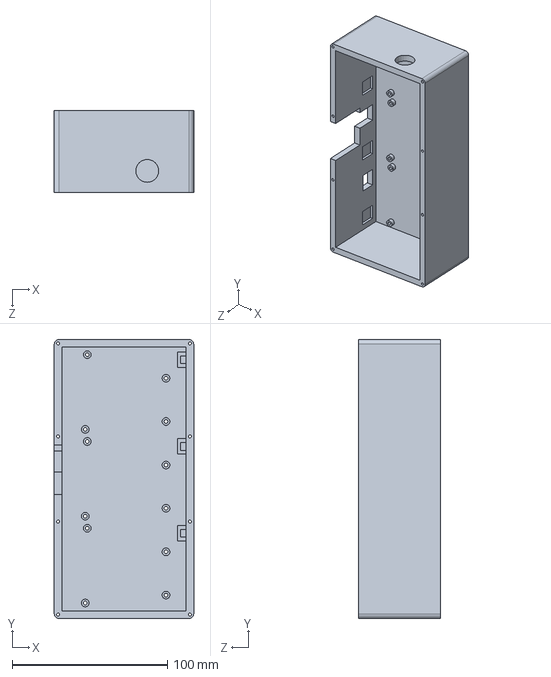
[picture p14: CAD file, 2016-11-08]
hardware/3d_models/dash_enclosure/STC_housing.sldprt
90.0 x 180.0 x 53.0 mm

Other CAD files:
hardware/3d_models/kia_soul/side_bracket.SLDPRT
hardware/3d_models/kia_soul/reservoir_bracket.SLDPRT
hardware/3d_models/brake_enclosure/brake_house_lid.SLDPRT
hardware/3d_models/brake_enclosure/brake_housing.SLDPRT
hardware/3d_models/brake_enclosure/actuator_control_board_enclosure_bottom.STL
hardware/3d_models/brake_enclosure/actuator_control_board_enclosure_top.STL
hardware/3d_models/brake_enclosure/brake_cable_clamp.SLDPRT
hardware/3d_models/brake_enclosure/brake_cable_clamp.STL
hardware/3d_models/brake_enclosure/brake_house_lid.STL
hardware/3d_models/brake_enclosure/brake_housing.STL
hardware/3d_models/dash_enclosure/STC_housing.STL
hardware/3d_models/dash_enclosure/STC_lid.STL
hardware/3d_models/estop_cupholder/EStopHousing.STL
hardware/3d_models/kia_soul/bottom_bracket.SLDDRW
hardware/3d_models/kia_soul/reservoir_bracket.SLDDRW
hardware/3d_models/kia_soul/side_bracket.SLDDRW

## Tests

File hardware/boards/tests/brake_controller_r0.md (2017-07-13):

# Brake Controller Revision 0 Test Plan

The tests for the Brake Control module are split into three parts: Bench,
installation and integration testing. The bench tests ensure the module itself functions as expected
and the installation tests ensure the module is integrated correctly.

## Microcontroller Testing

1. Supply a stable voltage to the microcontroller via USB and check the Arduino using the
blink tutorial.

2. Confirm the correct voltages at the supply voltage pins (0V, 3.3V and 5V)
using a digital multi-meter thus checking the voltage level converter.

3. Attach the Brake Control board to the Arduino, supply 12 volts to the
module using the screw terminals and verify the blink tutorial runs.

4. Upload the test firmware to Arduino and connect the test harness. Run the
interactive tests which test:
  - Power
  - PWM drivers
  - Pump relay
  - Brake light switch relay
  - CAN send/receive

## Installation Testing
These tests are to be run while the Brake Control module is connected to a computer
via a USB cable. These tests are to be run with the vehicle off the ground
so that the wheels can turn freely.

1. Install the Brake Control module into the vehicle.

2. Initiate the in-vehicle test routine to test:
 - Power
 - Accumulator pressure
 - Brake pressure control
 - Brake pedal input sensing

3. Upload the Brake control firmware.

4. Using a laptop, command the vehicle to brake. Press on the brake pedal and ensure
that the brake module disables control.

5. While the control modules is braking the vehicle, press the emergency stop button and
check that normal braking is possible.

## Integration Testing
These tests are to be run with the vehicle off the ground so that the wheels can
turn freely. All other modules should be installed in the vehicle and
connected via the Control CAN bus.

1. Using the joystick commander utility, enable control and brake the vehicle.

2. Quit the joystick commander utility and check that the brake module disables control.

3. Using the joystick commander utility, enable control and brake the vehicle.
While braking, press the soft-stop button and check that normal braking is possible.

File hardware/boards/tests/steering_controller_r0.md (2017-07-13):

# Steering Controller Revision 0 Test Plan

The tests for the Steering Control module are split into three parts: Bench,
installation and integration testing. The bench tests ensure the module itself functions as expected
and the installation tests ensure the module is integrated correctly.

## Microcontroller Testing

1. Supply a stable voltage to the microcontroller via USB and check the Arduino using the
blink tutorial.

2. Confirm the correct voltages at the supply voltage pins (0V, 3.3V and 5V)
using a digital multi-meter thus checking the voltage level converter.

3. Attach the Steering Control board to the Arduino, supply 12 volts to the
module using the screw terminals and verify the blink tutorial runs.

4. Upload the test firmware to Arduino and connect the test harness. Run
the interactive tests which test:
  - Power
  - DAC
  - Signal interrupt switch relay
  - CAN send/receive

## Installation Testing
These tests are to be run while the Steering Control module is connected
to a computer via a USB cable. These tests are to be run with the vehicle off
the ground so that the wheels can turn freely.

1. Install the Steering Control module into the vehicle.

2. Initiate the in-vehicle test routine to test:
 - Power
 - Signal interrupt switching
 - Steering spoofing
 - Steering sensing

3. Upload the Steering Control firmware.

4. Using a laptop, command the vehicle to steer. Turn the steering wheel and ensure
that the steering module disables control.

5. While the control modules is steering the vehicle, press the emergency stop button and
check that normal steering is possible.

## Integration Testing
These tests are to be run with the vehicle off the ground so that the wheels
can turn freely. All other modules should be installed in the
vehicle and connected via the Control CAN bus.

1. Using the joystick commander utility, enable control and steer the vehicle.

2. Quit the joystick commander utility and check that the steering module disables control.

3. Using the joystick commander utility, enable control and steer the vehicle.
While steering, press the soft-stop button and check that normal steering is possible.

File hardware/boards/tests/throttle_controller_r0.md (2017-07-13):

# Steering Controller Revision 0 Test Plan

The tests for the Steering Control module are split into three parts: Bench,
installation and integration testing. The bench tests ensure the module itself functions as expected
and the installation tests ensure the module is integrated correctly.

## Microcontroller Testing

1. Supply a stable voltage to the microcontroller via USB and check the
Arduino using the
blink tutorial.

2. Confirm the correct voltages at the supply voltage pins (0V, 3.3V and 5V)
using a digital multi-meter thus checking the voltage level converter.

3. Attach the Steering Control board to the Arduino, supply 12 volts to the
module using the screw terminals and verify the blink tutorial runs.

4. Upload the test firmware to Arduino and connect the test harness. Run the
interactive tests which test:
  - Power
  - DAC
  - Signal interrupt switch relay
  - CAN send/receive

## Installation Testing
These tests are to be run while the Throttle Control module is connected to a
computer via a USB cable. These tests are to be run with the vehicle in park.

1. Install the Throttle Control module into the vehicle.

2. Initiate the in-vehicle test routine to test:
 - Power
 - Signal interrupt switching
 - Throttle spoofing
 - Throttle sensing

3. Upload the Steering Control firmware.

4. Using a laptop, command the vehicle to accelerate. Pressed the
accelerator pedal and ensure that the throttle module disables control.

5. While the control modules is accelerating the vehicle,
press the emergency stop button and check that normal throttle function is restored.

## Integration Testing
These tests are to be run with the vehicle in park. All other modules should be
installed in the vehicle and connected via the Control CAN bus.

1. Using the joystick commander utility, enable control and accelerate the vehicle.

2. Quit the joystick commander utility and check that the throttle module disables control.

3. Using the joystick commander utility, enable control and accelerate the vehicle.
While accelerating, press the soft-stop button and check that normal throttle function is restored.

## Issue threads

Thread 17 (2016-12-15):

Estop STL file

droter, 2016-12-15:
I tried printing the estop stl file on a makerbot mini and it isn't able to print.

Has anyone tried printing this file?

ltbj, 2016-12-15:
At what point does the print fail?

Does the makerbot software generate the gcode from the STL properly?

Any other info you can provide would be helpful!

I'm not familiar with the makerbot mini, though it does have a fairly small print bed, only 4 x 5 inches. I'll take another look at the model and check the size.

droter, 2016-12-15:
It may be a problem with the maker bot.  It fails at the very beginning stalls on 77% after homing.  We are trying the export from solid works again.

There isn't any error messages.  I can test it again.

droter, 2016-12-20:
Must be something with the makerbot mini and orientation of the part.  We flipped it over so the switch holes were on top and it printed okay.

Closed 2016-12-20.

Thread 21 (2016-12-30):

Steering in higher speeds

zwn, 2016-12-30:
Can you please elaborate more on the steering implementation? AFAIU the power steering in most vehicles is active only in slow speeds. In higher speeds it disengages since it is not needed (and might even be counterproductive). Is the Kia Soul steering implementation different?

In the [CAN Specification](https://github.com/PolySync/OSCC/wiki/CAN-Specification) I see a Steering Command - is the steering completely mechanical decoupled? I mean is it steer-by-wire? Or is there something else in the design I am missing?

evanlivingston, 2016-12-30:
@zwn The steering system in the Kia Soul is an electronic power steering system. The steering column has a DC motor, redundant torque sensors and a steering microprocessor. When a driver turns the steering wheel the torque in the column increases. The steering microprocessor then attempts to reduce the torque by powering the DC motor in the direction of the torque.

By placing the steering module between the torque sensors and the steering microprocessor, OSCC can cause the steering microprocessor to steer the vehicle.

The CAN Steering Command messages are interpreted by the OSCC steering module, which translates the CAN messages into analog voltages then supplied to the steering microprocessor. The Steering Command messages are not sent to any Kia microprocessor, they are only available to the OSCC modules.

zwn, 2017-01-01:
Did you have a chance to test your implementation at speeds above 30km/h? I am wondering if the Kia steering microprocessor stops the assisting when a certain speed is reached as that is the behavior to expect when the car is driven by a human.

zwn, 2017-01-01:
I have not been able to confirm that the Kia contains a true steering-by-wire system. It seems to be only electric power assisted steering (EPAS) system. For example the page
http://www.kisouman.com/electric_power_steering_eps_-465.html
suggests the motor might turn off to prevent its overheat and there might be other conditions as well. The loss of the power assistance is not treated as a dangerous situation which makes sense. It would be dangerous only in lane keep assist system.

I think the only car on the market with steer-by-wire is Infinity Q50. But I would love to be proved wrong :smile:

Closed 2016-12-30.

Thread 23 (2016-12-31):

Tests contain a lot of uncalled and commented-out code.

galv, 2016-12-31:
The test cases are currently really shabby. I'm not quite sure what they're meant to be doing right now. It seems almost as if they're supposed to be somehow interactive, but they're currently cluttered with commented out regions and unused functions.

Not sure how to resolve this issue. I just wanted to bring this up to the maintainers too understand what the goal is of the tests.

ltbj, 2017-01-04:
We can resolve this by cleaning up the existing code and adding useful comments -- changes will be pushed up soon and we'll come back to this issue with a PR.

ltbj, 2017-01-19:
This is addressed in the `bugfix/standardize-pid-library` branch, which will be pull-requested early next week once we tune the new code and validate the changes on the brake board.

Validation on the steering board is complete, and the throttle board does not use the PID library.

I'll leave this open until the PR gets through, and we have improved in-line code comments to descibe what tests should be doing, and where they are run.

Closed 2017-01-31.

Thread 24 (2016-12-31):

Duplication between `firmware/*/kia_soul_ps/*.ino` and `firmware/tests/*.ino`

galv, 2016-12-31:
There is a lot of duplicated constants between the actual firmware files and the test firmware files right now. I would really like to see these factored out into a common file that gets #included into these files instead. For example, `CAN_BAUD`, `SERIAL_BAUD`, and `CAN_INIT_RETRY_DELAY` get #defined everywhere to the same values. My experience is that you will probably never have any reason for these to be different between different boards (especially the serial and can bauds), anyway. And right now, as soon as you change something in the firmware, the tests could break, which is a headache.

I would like to see a common.h file that defines the above three constants, as well as a few others I'm not thinking of right now, and .h files for each type of board defining GPIO pin names, so we can rid ourselves of this duplication.

Also, I don't want to put multiple issues into the same github issue, but I realize now that the tests/ directory does not have the same directory structure as the rest of the code. i.e., there are no kia_soul_ps/ directories, even though the test there right now clearly (?) apply only to the kia soul.

lpdon, 2017-01-01:
Is there also any reason to have more than one PID code? OSCC/firmware/steering/kia_soul_ps/PID.* and OSCC/firmware/arduino_libraries/PID_v1/?

LucasBuckland, 2017-01-05:
Thanks for the input here guys. We have discussed this internally and will be adding a common.h file as well as standardizing the PID library etc in the near future.

evanlivingston, 2017-01-10:
@galv: Don't hesitate to create multiple issues.

The tests/ directory has slightly different structure because some tests are designed for the boards themselves rather than a car installation. The boards should have tests that can verify their core functionality separate from their functionality inside of a vehicle.

ltbj, 2017-01-19:
The `common.h` file was added and related changes were made in this PR: https://github.com/PolySync/OSCC/pull/38

galv, 2017-01-19:
@evanlivingston

Is the intent that each PCB/arduino shield be able to interface to cars besides the Kia soul without having to refabricate the PCB? I haven't dug into their designs much, but was wondering about whether the team made that design decision.

ltbj, 2017-01-31:
You're right, the OSCC modules will work for other vehicles that have by-wire steering and throttle control modules that require voltage spoofing on redundant sensors.

We are currently looking at other vehicles that OSCC will be able to support, starting with other Kia models, specifically the Kia Niro.

Closed 2017-01-31.

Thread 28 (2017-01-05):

Where to source parts for Brake installation

droter, 2017-01-05:
Hi,

I haven't been able to find plugs and brake lines to add the redundant brake.  Is there some place online where I can by the plugs and lines?

Thanks,

Matt

anathan, 2017-01-06:
Try Jegs or Summit Auto

-Aaron

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

droter, 2017-01-06:
Thanks Aarron,

Do you know the part size of the plugs?  Are they 10mm x 1.25 inverted?  Also, what are the lengths of the brake lines?

Matt

evanlivingston, 2017-01-06:
Matt,

We are working on creating a better BOM for these parts. The plugs for the brake actuator are -3. We use two 48" -3 brake lines and two 26" -3 brakes lines. 4 M12x1.0 inverted flare to -3 and 6 M10x1.0 inverted flare to -3 adapters are needed. After looking yesterday it looks like most of these parts are available from jegs and Summit Auto, except I haven't been able to find a reliable source of the adapters yet. If you find one please let us know so we can add it to the BOM.

droter, 2017-01-09:
Here are the parts I have found:

M10 1.0 inverted to -3 http://www.jegs.com/i/Russell/799/641431/10002/-1
48" Brake Line  http://www.jegs.com/i/Earls/361/63010148/10002/-1
26" Brake Line  http://www.jegs.com/i/Earls/361/63010126/10002/-1

Haven't been able to locate the M12 1.0 to 3 yet.

evanlivingston, 2017-01-10:
M12x1.0 to -3 Is a bit more rare. Supposedly Aeroquip makes them but I can't find a part number. Autobahn88 makes the part. Their part number is FTSS002-AN3-M121.

https://www.amazon.com/Autobahn88-Stainless-Steel-Fitting-Adapter/dp/B019RVZZ16

evanlivingston, 2017-01-10:
Okay, We have an updated and complete BOM for the brake install. Head over to https://github.com/PolySync/OSCC/wiki/Brake#hardware to check it out.

Closed 2017-01-10.

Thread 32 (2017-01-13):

Brake Module Box

droter, 2017-01-13:
Has anyone found a place to buy a brake module enclosure?

The 3d printed file will cost around $359 on shapeways.  The STC lid and box are around $170.

Is there some other enclosure we can use?
Thanks,

Matt

evanlivingston, 2017-01-13:
@droter:

The enclosure for the brake module currently in the repo is for the prototype board.

The new board is significantly smaller. I'm redesigning the enclosure today and doing test prints. The new enclosure should be cheaper to print but I agree an alternative should be found. We will spend some time here looking for project boxes that can accommodate the modules.

Evan

droter, 2017-01-18:
Would these type of boxes work:
http://www.graybar.com/store/en/gb/non-metallic-junction-box-93172343

evanlivingston, 2017-01-19:
Those work great. We used those for our prototypes.

The board to control the brake actuator is 4"x8"x2.5"

Closed 2017-01-20.

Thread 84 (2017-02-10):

Steering control should have a timeout for chassis_state_1 frame

evanlivingston, 2017-02-10:
The steering code depends on getting the steering angle from the C-CAN bus via the OBD-II connector. Currently, the firmware does not have a timeout for receiving the CAN frame that contains the steering angle. If the controller does not receive steering angle for any reason (disconnected OBD cable) then the steering controller runs but errantly.

petebrink, 2017-02-10:
This is going to required that we determine if there is any regularity to this message.  If the message does not get sent when the steering wheel is static, then it is impossible to determine if there has been a timeout.

Recommend doing some empirical testing to determine what the update rate for the chassis message is.

joshhartung, 2017-02-10:
IIRC they come at a 10ms update rate with very little jitter.

LucasBuckland, 2017-04-10:
This has been added to our backlog of tasks and will be addressed in the near future.

austinjmorlan, 2017-06-01:
Resolved with #133.

Closed 2017-05-30.

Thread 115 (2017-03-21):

Throttle CS pins in code don't match schematics

hkorre, 2017-03-21:
Throttle code:
https://github.com/PolySync/OSCC/blob/devel/firmware/throttle/kia_soul_ps/throttle_control_module.ino#L49-L55
* #define CAN_CS                          ( 10 )
* #define DAC_CS                          ( 9 )

Schematic:
https://github.com/PolySync/OSCC/blob/devel/boards/sensor_interface_board/sensor_interface_board_sch_1.0.0.pdf
* Pin10 -> CS_A -> DAC_CS
* Pin11 -> CS_B -> CAN_CS

Seems to me that the schematic is incorrect.

This is all on 'devel' branch

dan-fern, 2017-03-21:
Hasan,

Thanks for pointing this out.  The diagram and firmware are both accurate in fact.  I think you mistook the pin number on the integrated circuit block to be the destination pin on the Arduino.  The Arduino pinouts are labeled on the inside of the `ARDUINO_JP1` block in zone C6 where `CS_A` runs to `D9` and `CS_B` runs to `D10`.  In Zone A3/A4, you'll see `CS_A` go to `MCP4922T`, which is the [DAC P/N](http://www.digikey.com/product-detail/en/microchip-technology/MCP4922T-E-SL/MCP4922T-E-SLCT-ND/736003).  In turn, `CS_B` goes to `MCP2515` in zone A6, which is the [CAN controller](http://www.microchip.com/wwwproducts/en/en010406).  I can see how it is confusing when the pin number and pin destination are offset by one.

Best regards,

Daniel

hkorre, 2017-03-23:
@dan-fern: Thanks so much for clarifying!

Closed 2017-03-21.

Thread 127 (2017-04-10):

Vehicle vibration causes screw terminals to loosen

LucasBuckland, 2017-04-10:
In our testing we have noticed that screw terminals on the OSCC boards can loosen due to vibration. We are working on a long term solution to address these issues in our newer model boards. For all existing boards we highly recommend applying blue loctite to all screw terminals, and checking that terminals are properly tightened. Loose connections can cause power steering or throttle to fail, or the added Prius brake actuator to not function as expected.

Closed 2017-10-30.

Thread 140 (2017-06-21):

Supported Kia Soul models?

MohammadAbuQare, 2017-06-21:
Hi,

Does OSCC support Kia Soul 2017?
What are the supported Kia Soul models (LX, EX, SX) ?
Does it need to have Auto Parking Assistant?
Is there any modification or requirements needed?

MQ

jweatherson, 2017-06-22:
Hi MQ,

The kit does support the 2017 Kia Soul and the LX, EX and SX models all work with the kit.  It does NOT need to have Auto Parking Assist.

Modifications to the brake lines are required when adding the Toyota brake controller.  In addition, without the factory connectors, it is required to splice into the steering column torque sensors and throttle position sensors.

Thanks,
James

waiwnf, 2017-06-30:
Dear PolySync people, I am trying to extend your work (only wrt steering for now) to the European KIA Cee'd, but am having some issues. So I would appreciate if you could share some details on your setup:

1. What is the steering column part numbers you are working with? Is that 56310B2000 for the column and 56340B2000 for the MDPS ECU?

2. I have a 2012 Cee'd steering column with MDPS (part 56300A2000) with MDPS ECU connectors to the sensors and steering drive shown at this diagram http://kiaceed2.ru/shemy/el-us.png . Does that look similar to what you are working with?

Apparently the number of wires is different on the Cee'd (7 vs 6 for Soul). There wires for VTAS, TS4 (?), SAS1, SAS2, TSS, Ground and +5V. What puzzles me is that (at rest) from SAS1 comes +5V and from SAS2 comes 0V, which does not match your plot for torque sensor voltages. Also both TS4 and TSS produce 0.

3. Have you tried "booting up" power steering separately on a test bench without a car? I don't have the car itself, and apparently MDPS expects to hear certain CAN frames on the bus before actually enabling the steering assist - just connecting ignition is not enough. If you have CAN dumps for the vehicle start, could you share those so that I can try to fool the MDPS ECU into working?

Thank you, and really appreciate your sharing this project with the community!
-Anton

k-cleary, 2017-07-03:
Those look like the same part numbers that we have on our cars. It sounds like you may have a different connector, or are possibly measuring different pins.
We don't know much about that model of KIA, so you will need to reverse engineer it yourself. The torque sensor pins will change their voltages when the steering wheel is turned, which should help you identify which pins you need to be reading from.
We've only ever tested the steering on the vehicle, so we don't know that specific CAN sequence. You'll have to find it yourself, which may be a bit tricky.
Thanks for reaching out, and we're excited to see what you can come up with!
-Katie

waiwnf, 2017-07-04:
Great, thanks for the update!

yapjiaqing, 2017-08-15:
Dear PolySync people, what's the difference between the systems of the Kia Niro and the Kia Soul to take note of, that affects the use of the OSCC development kit? We'd like to do all we can on the vehicle first while waiting for Kia Niro support to be out at the end of the year

nathanaschbacher, 2017-09-25:
Howdy,

From our initial testing at the actuation-level the Niro's steering control is different enough to require doing more work determining where to properly tap into the system to enable OSCC.

On the data side of things, the Niro's OBD II port also behaves differently than either the Soul or Soul EV, so there's work for us to do there to make sure we can properly read and parse relevant data from the vehicle.

The soon-to-be-available OSCC hardware updates that support the Soul EV look like they'll also be compatible with the Niro and that the differences will likely be only in firmware updates, but there's still some more work to do for us to be 100% certain.

fabio71c, 2019-07-12:
Anyone using comma ai Openpilot / OSCC on a Kia 2015 ?
I have a Kia 2015, I have bought the EON ( Openpilot ), yet since the car didn't come with ACC or KLAS, I'm looking into the OSCC kit.  Would be great to hear if anyone has done such project. Thanks.

Closed 2017-09-25.

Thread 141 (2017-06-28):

Questions related to wiring and installing the platform

ubgit009, 2017-06-28:
I figured it would be easier for people to look at the questions if they were posted as separate issues.

Hi everyone,
I don’t mean to be annoying with so many questions, but honestly I’ve spent quite a bit of time going through the Wiki pages, and there are a lot of things I am confused about related to wiring and installing the platform. I don’t have much of a background assembling wire harnesses or working under the car hood, so more detailed instructions would be greatly appreciated. I bet more people trying to use this platform feel the same way.
So here are the questions.
1.	How much current (approximately) should be allocated for the entire system (including sensors/future modules)?

2.	As far as power distribution, there seem to be some inconsistencies between the schematic in the Overview page and the one in the Power Distribution page.
Specifically:
-In the “Overview” page, power to the entire system is controlled by both the System Switch and the Emergency stop, whereas in the “Power Distribution” page the CAN gateway and the sensors are independent from the Emergency Stop.
-In the “Overview” page there is a relay and the Fuse Box separating the System Switch from the Emergency stop, whereas in the “Power Distribution” page the two are connected directly.
-In the “Overview” page, there are separate fuses to control how much current can flow to the Brake Module and the other modules, whereas in the “Power Distribution” page all 3 modules receive power from wires branching out of a single relay.
-In the “Overview” page wires of 20 awg gauge are indicated for the +12V and ground connections to the modules, whereas in the “Power Distribution” page 22 awg is indicated.
I can’t think of other inconsistencies at this point, but if you examine the two schematics closely, I’m sure you can find more.
Can you please clarify which schematic should be followed?

3.	From the schematic in the Overview Page

 3a. Are the 200 A fuse and relay closest to the battery already in the car? If not, can you include a link to good parts we can buy online?

3b. How are we supposed to install and connect the System switch, the 200 amp relay and fuse (assuming the latter two are not already in the car) between the battery + terminal and the Fuse Box?

 3c. Are all the fuses and relays in the schematic supposed to go inside the engine compartment? If so, how do we mount them and what tools/parts do we need?

3d. I see the word ‘glovebox’ in parenthesis for the Deutsch connectors. Are the connectors already there? Or is it just a suggestion to put them there along with the modules?

4.	From the schematic in the Power Distribution Page

4a. What are the amp rating requirements for the fuses and relays?

4b. How do we mount the fuses and relays? I know the page says something about using Seaboard. But can you be more specific about the tools/parts/procedure?

5.	Where are the steering, throttle and gateway modules supposed to go? Inside the glovebox? And how do we run wires from the engine compartment to wherever the modules are supposed to go? Please be specific.

6.	How do you do a proper splice between a wire of a larger gauge, into two or more of a smaller gauge (tools/parts and procedures) ?

7.	How do you access the Break Pedal Switch and the junction and run wires to the OSCC brake module?

8.	Installing the steering and throttle modules requires cutting a pair of wires for each:
   2 wires that connect the torque sensor and EPAS ECU for the steering, and 2 wires that connect the Accelerator Position Sensor and the Throttle Body for the throttle. But what if somebody wants to remove the modules from the car? Would it make sense to terminate the cut wires coming out each sensor and unit with matching plug/receptacle of a Deutsch connector. Or how would you restore the car to its original configuration?

9.	How do you build the Control CAN Bus that will connect the gateway, OSCC modules and the control computer? As I understand, the bus needs to be terminated at both ends with 120 Ω. What connectors/cables/wires/terminators do we need?

10. What about the possibility of installing all the hardware in the back of the car  . Would that be feasible? How should we do the wiring?

dan-fern, 2017-06-29:
Thank you for your interest in OSCC.

The OSCC platform does not include any sensors in the system diagram you've referenced.  Any sensor payload that you were to design would require its own power budget to be added upon the base OSCC system.  For reference, however, in-house testing has shown an Alienware Aurora R6 with 2 nVIDIA GTX1070 GPU's running alongside the complete OSCC kit drew a peak load of 200W.  This was captured running on an AC inverter powered off the vehicle battery and stock Kia Alternator (~85A).

The "Power Distribution" diagram you referenced is outdated and will be replaced when we redesign the wiki next month.  The "Overview" diagram shows the entire system being controlled by the system switch as you mentioned.  It is the more up-to-date system diagram and it contains all the fuse amp ratings and suggested wire gauges.  You should refer to that diagram if you are planning to build a car.

The hardware described in the "Overview" diagram is mostly non-stock.  Many non-OSCC components are off-the-shelf and can be found at popular electronics and mechanical suppliers, with the exception of a few custom mounting brackets and 3D-printed enclosures.  The diagram is listed with suggested locations for 3rd party hardware, but the design is ultimately up to you.  One suggested mounting location is the spare wheel well in the trunk as there is plenty of space to mount hardware and is easy to conceal.  I would also suggest to remove the door trim and run added wiring along stock harnesses.

The splices into the stock wiring are meant to be permanent.  You could, however, use a different set of Deutsch connectors to reconnect cut wiring and restore the vehicle to it's factory state.  Please reference a Kia parts manual for locations to the brake light switch, torque sensor, EPAS ECU, and Accelerator Position Sensor.  For information about how to splice wires of different gauges, please reference an online tutorial.  The general rule is to add the conductor diameters up for each side and use a splice which fits the summed diameters.

Thank you for raising these points around the complexity of integrating the OSCC kit into a vehicle without much prior knowledge of electrical harnesses or vehicle systems.  In the near future we will announce a complete OSCC “in-a-box” install kit for clients that want a turn-key platform solution.  That option will include all the hardware, components, wiring harnesses, and documentation necessary to build a OSCC vehicle.  For more information you should reach out via email to oscc-orders@polysync.io

Closed 2017-06-29.

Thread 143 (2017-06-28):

The correct schematic for the power distribution

ubgit009, 2017-06-28:
As far as power distribution, there seem to be some inconsistencies between the schematic in the Overview page and the one in the Power Distribution page.
Specifically:
-In the “Overview” page, power to the entire system is controlled by both the System Switch and the Emergency stop, whereas in the “Power Distribution” page the CAN gateway and the sensors are independent from the Emergency Stop.
-In the “Overview” page there is a relay and the Fuse Box separating the System Switch from the Emergency stop, whereas in the “Power Distribution” page the two are connected together.
- In the “Overview” page, there are separate fuses to control how much current can flow to the Brake Module and the other modules, whereas in the “Power Distribution” page all 3 modules receive power from wires branching out of a single relay.
- In the “Overview” page wires of 20 awg gauge are indicated for the +12V and ground connections to the modules, whereas in the “Power Distribution” page 22 awg is indicated.
I can’t think of other inconsistencies at this point, but if you examine the two schematics closely, I’m sure you can find more.
Can you please clarify which schematic should be followed?

dan-fern, 2017-06-29:
Closed per #141

Closed 2017-06-29.

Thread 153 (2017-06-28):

Using the car without the modules after cutting wires from the torque and accelerator sensors.

ubgit009, 2017-06-28:
Installing the steering and throttle modules requires cutting a pair of wires for each:
   2 wires that connect the torque sensor and EPAS ECU for the steering, and 2 wires that connect the Accelerator Position Sensor and the Throttle Body for the throttle. But what if somebody wants to remove the modules from the car? Would it make sense to terminate the cut wires coming out each sensor and unit with matching plug/receptacle of a Deutsch connector. Or how would you restore the car to its original configuration?

dan-fern, 2017-06-29:
Closed per #141

Closed 2017-06-29.

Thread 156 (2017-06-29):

Need a few more clarifications from the “Overview" Page Diagram

ubgit009, 2017-06-29:
Thank you Dan for answering my first set of questions. Now that we know the diagram in the “Overview” page is the one to be followed, I’m hoping a few more things can be clarified.

1. Where in the Fuse Box, should the wires going to the 200 amp relay and the Emergency Stop be connected?

2. There are two wire branches coming out of the + terminal in the battery: one is 4 awg and the other 12 awg. Is the diagram implying that we connect two separate lug terminals of different gauges to the battery terminal?
3. The 200 A fuse, 200 A relay and the System Switch are closer to the + terminal of the battery, than the Fuse Box. Does that mean we need to cut and splice any stock power wires from the Kia Or how do we connect those 3 elements between the battery terminal and the Fuse Box?

4. For any component that connects to ground. Is it better to find a local ground point and try to make a connection there, or to wire it back to the – terminal of the battery? Take as examples the 200 amp  and 40 amp relays, as well as the two pins in the Brake Actuator.

dan-fern, 2017-06-29:
The "fuse box" listed in the "Overview" diagram refers to an added 3rd party fuse block; it does **not** refer to the stock Kia fuse box.  I would suggest finding a fuse block to distribute the +12VDC power from the battery/alternator.  It should serves as a shared grounding point for OSCC hardware, all of which should be then be grounded at the same chassis ground point as the negative battery terminal.  I would also suggest finding a circuit breaker to separate the battery (line) from all the OSCC hardware (load).  I hope that helps.

Thanks for your continued interest in OSCC.

ubgit009, 2017-07-04:
Once again, my intention is not to annoy you with a lot of questions. I just want to get past the hardware installation so that I can focus on other aspects of the project.
I have a few remarks referring to the same diagram:
  1) You mention the fuse box should be used to distribute power, but  in the diagram all I see is a single wire coming in and a single wiring coming out. And there are fuses for all the modules elsewhere in the schematic. So what exactly is supposed to go inside that fuse block?
   2) It was mentioned in a previous issue that the system, with more hardware in addition to the OSCC modules and gateway used about 85 A. But the 2nd relay (the one that is controlled by the Emergency stop) is rated for 40 A. Is that right? Where is the additional amperage suppose to come from?
  3) If I may make a suggestion. Why not update the "Overview" page to include a list of all suggested parts (along with links to vendors) needed to implement the system on the diagram? I'm sure that will make life easier for a lot of people.

Closed 2017-06-29.

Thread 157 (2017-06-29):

About the Control Can Bus Physical Implementation

ubgit009, 2017-06-29:
How do you build the Control CAN Bus that will connect the gateway, OSCC modules and the control computer? As I understand, the bus needs to be terminated at both ends with 120 Ω. What connectors/cables/wires/terminators do we need?

dan-fern, 2017-06-29:
Once you assemble all the OSCC modules, you'll need to connect the CAN Gateway Module to a control computer, or ECU.  This ECU will be used to issue commands to the steering, throttle, and brake modules.

This is a [great overview on CAN networks](http://www.ti.com/lit/an/sloa101b/sloa101b.pdf) from Texas Instruments.  I hope that helps.

Thanks for your continued interest in OSCC.

ubgit009, 2017-07-04:
Thanks for sharing that link to Texas Instruments guide on CAN networks. I'm understand how CAN network goes as far as the frame formats, and the overall architecture .  I'm more confused about how to physically connect all the wires. Unfortunately, the guide from Texas Instruments doesn't address that topic in a lot of detail.

Let me be a little more specific:
 1) How do we connect 3 or more nodes  ( i.e. the OSCC 3 modules and the Gateway) to the same CAN wire? Should we do soldered or crimped tap joints?

 2)Do we need any specific connectors for each node, or bare 20 awg wires would be sufficient? I noticed the DB-9 is popular even though half of its pins are left unused.

 3 According to the  ISO 11898-2 standard, which specifies physical Layer for a  high speed CAN bus, the CAN H and CAN L should be terminated at two **and** **only** two nodes with 120 ohm resistors.
I noticed from the schematics that  the CAN Gateway, the OSCC sensor shields and the brake actuator control board are all terminated with a 120 ohm by default. Do we need to make any changes to the boards, so that only two nodes have the CAN wires terminated? I also read about using separate terminators so that nodes can be removed without electrically compromising the bus.

 4) Do we need a specific cable?
Appropriate wire gauge? ? Shielded vs Unshielded cable? Characteristic impedance?
 What about the cable shield carrying the reference ground? Please see Figure 1.3.1 and Figure 1.3.2 on page 4 of the following article and you will see what I'm talking about:
http://canlab.cz/pages/download/CAN-Wiring.pdf

Closed 2017-06-29.

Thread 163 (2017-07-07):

Adding a Parts list in the "Overview" page

ubgit009, 2017-07-07:
I know it was mentioned previously that the Wiki is going to updated in the next month., but one thing I think it would be super helpful and would save a lot of time to some people is to have a parts list available . Is there any way, you could PLEASE provide a list of all the parts (with online links when available) needed to implement the diagram from the "Overview page"

LucasBuckland, 2017-07-07:
Thank you for your questions. I want to start out by saying that this repo is intended as a resource for the general application of the OSCC boards as a research platform. It is not intended to be a detailed installation guide. A certain level of vehicle electrical systems knowledge is necessary to properly install the basic OSCC board kit into a vehicle. For customers that require a turn-key solution, we will soon be offering complete installation kits that will include all the hardware, wiring harnesses, and documentation necessary for a simple and straightforward installation. You won’t even need to splice into the vehicle wiring harness.

As Katie mentioned earlier, a revamp of the wiki is underway that will make the useful boundaries of the repo more clear, with better organization and better labeled diagrams. However, as I’ve mentioned, this is a general-use / reference design resource so it won’t include a fully detailed installation guide. To get you started, I’ve listed some resources below that should give you a good basis of understanding for automotive electrical systems and proper methods of wiring. We’ll be adding these resources (and more) to the redesigned wiki. And, again, we’re going to be announcing a lot more around the OSCC product that will significantly ease installation.

Wiring:
    http://www.onallcylinders.com/2013/12/05/wiring-101-basic-tips-tricks-tools-wiring-vehicle/
CAN Wiring:
    http://www.cowfishstudios.com/blog/canned-pi-part1
Twisted pair:
    https://www.electronics-notes.com/articles/constructional_techniques/hints_and_tips/how-to-make-twisted-pair-wire.php
CAN network overview:
    http://www.ti.com/lit/an/sloa101b/sloa101b.pdf
Soldering technique:
    https://www.sciencebuddies.org/science-fair-projects/project_ideas/Elec_primer-solder.shtml#soldering
Vehicle electrical system basics:
    https://www.howacarworks.com/basics/how-car-electrical-systems-work
Adding a device onto vehicle power circuit
    http://www.instructables.com/id/How-to-Add-a-Circuit-to-Your-Car/
Car Wiring Tips:
    https://www.lifewire.com/diy-car-wiring-tips-534682

Closed 2017-07-07.

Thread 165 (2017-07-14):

Basic Electrical Specifications of the OSCC Sensor Interface and Brake Actuator Boards

ubgit009, 2017-07-14:
I realize the Wiki is not intended to be an official source of instructions for installing the kit. Hence, for the purpose of selecting appropriate wire gauges, fuses ratings, and other suitable components to build a power distribution circuit could you please share some of the **basic electrical parameters of the sensor and actuator control boards**?

I'm looking for basic things such as...

-Vin range at which each board can function properly.
-Input resistance of each board.
-Min/Typical/Max Current used by
   (1) OSCC Brake Module
   (2) OSCC Gateway +  OSCC Throttle + OSCC Steeering combined
   when connected to the car modules.
-Any other data you thing would be helpful for the purpose I described above.

A few side questions on the "Overview Schematic".

I see the circuit is protected with a 200 Amp component next to the battery. Is that supposed to be a fuse or a circuit breaker? Or can it be either?

I did some research on automotive wire ratings by gauge. From what I understood,  there are multiple factors that determine how much current a wire of a given gauge can safely tolerate. However, I found a few articles suggesting that 200 A might be too much for a 4 awg wire. Is 4 awg, as shown in the diagram OK? Alternatively, would lowering the fuse/circuit braker and relay  rating to say about 100 A or 150 A still be acceptable for the application?

Is a 12 awg wire OK to supply power to the OSCC brake module?

Thank you for your continuous support.

LucasBuckland, 2017-07-22:
For both boards:
Vin = 6-26V (60V load dump protection and reverse bias protection)

Steering or throttle module: 60mA average up to  ~100mA.

The brake module pulls 300 mA average up to ~2.5A WITHOUT a brake actuator connected. The electrical characteristics of the Prius actuator can be found online; the actuator itself draws most of the current that goes into the brake module.

The input resistance would be based on what input you are measuring it at.

That system diagram is outdated and needs review, I would not rely on it to design a power system. It will be updated in the near future as part of our refresh of the wiki and documentation.

For your other questions please reference issue #163. In addition this link may be helpful.

http://www.engineeringtoolbox.com/wire-gauges-d_419.html

ubgit009, 2017-07-23:
Lucas,Thank you for the reply. I'm glad to know the Wiki refresh is on the works.  Our group has been stuck in the installation/ hardware setup phase for months and some of us are eager to make progress. Could you please give us a conservative timeline on when the Wiki Refresh will be completed and available to the public?

On Friday, July 21, 2017, 7:56 PM, Lucas Buckland <notifications@github.com> wrote:

For both boards:
Vin = 6-26V (60V load dump protection and reverse bias protection)

Steering or throttle module: 60mA average up to ~100mA.

The brake module pulls 300 mA average up to ~2.5A WITHOUT a brake actuator connected. The electrical characteristics of the Prius actuator can be found online; the actuator itself draws most of the current that goes into the brake module.

The input resistance would be based on what input you are measuring it at.

That system diagram is outdated and needs review, I would not rely on it to design a power system. It will be updated in the near future as part of our refresh of the wiki and documentation.

For your other questions please reference issue #163. In addition this link may be helpful.

http://www.engineeringtoolbox.com/wire-gauges-d_419.html

—
You are receiving this because you authored the thread.
Reply to this email directly, view it on GitHub, or mute the thread.

Closed 2017-09-25.

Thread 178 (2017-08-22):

Does OSCC suport 2017 KIA Niro Hybrid 1.6L DCT in China ？

dongjiahang, 2017-08-22:

nathanaschbacher, 2017-08-22:
Hi,

At the moment the Kia Soul ICE (internal combustion engine) platform is the only vehicle officially supported.

However, coming in the next few weeks the OSCC firmware and sensor interface board designs will be updated with support for the Kia Soul EV. The EV platform won't require the brake actuator installation procedure because we've figured out how to control the factory braking system in the EV, which saves a lot of .

Support for the Kia Niro Hybrid platform is currently on our roadmap to be completed and shipped before the end of the year, but we're always interested in finding development partners to accelerate our timeline for supporting new vehicles. We expect the Niro to be similar to the Soul EV in terms of ease of integration, but provide a driving-range closer to that of the Soul ICE, which is why we're excited to try to support it after we get the EV platform support released.

Soul ICE support will also continue for people who need a versatile long-range platform that is widely available globally today.

Does this also address issue #177 that you created?

dongjiahang, 2017-08-23:
What you mean is that the current open platform does not support Niro？Hardware does not support ？Or software does not support?

nathanaschbacher, 2017-08-23:
In this case both the hardware and the software don't support the Niro. That support is expected to be available before the end of the year (2017). We haven't brought a Niro into the shop to fully characterize the Niro's interfaces, so that we can determine what modifications need to be made to the hardware and/or the software to support it.

Early testing indicates that the Niro will probably be generally similar to the Soul EV, but each platform has its own little differences we need to figure out and integrate into OSCC.

Closed 2017-09-25.

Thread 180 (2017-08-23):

What about control of the automatic transmission?

DmitryTgn, 2017-08-23:
I didn't find any information about switching the selector to position "D", "P", "R". Do you plan to implement control automatic transmission?

k-cleary, 2017-08-23:
Hey Dmitry,

While this is definitely an interesting idea, the Kia Soul requires mechanical actuation of the gear shift to change gears. Since it doesn't support shift-by-wire we aren't able to actuate that on this vehicle purely electronically with OSCC. We have spent some time investigating a viable shift-robot, but currently have no plans to implement this on our immediate roadmap. It isn't a matter of technical feasibility. It's a matter of time and prioritization for the use cases we see most commonly.

You can still use OSCC while the car is in Park or Reverse. It works the way you'd expect. There may also be CAN messages from the vehicle's OBD-II CAN that report the state of the transmission, but we don't currently track them at this time.

Cheers,
Katie

Closed 2017-08-23.

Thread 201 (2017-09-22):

Steering module not working as expected

ramanathanrm95, 2017-09-22:
I wired up and flashed all the modules without any errors.
I installed the joystickcommander package and followed the steps with no errors.
When I run the ./joystickcommand, the command window initializes and when I press start button, the values of steering, brake and throttle are displayed and when the left stick is toggled, the steering value updates, but after a second, program closes by giving disable controls message and there is no change in the steering wheel position of the car even when the values are updated.

I built the can-gateway module by stacking 2 CAN shields and connecting one of them to Kvaser converter and then to laptop (Modified CS pin of one of the shields to pin 10 --> Connected to Kvaser converter, did not change the resistor)
Connected the steering module as given in GitHub.
Powered all the modules through the laptop itself.
Connected the joystick to the laptop.

Should there be a control can bus separately or can I just use the laptop as control can bus?

This is my current connection:

STEERING --> CAN GATEWAY --> OBD CAN
LAPTOP (CONTROL CAN) --> KVASER --> CAN GATEWAY
ALL MODULES POWERED THROUGH ARDUINO connected to LAPTOP
I don't have a physical control can bus. I am assuming my laptop will function as a control can bus.
No non-e power source.

Please let me know where I am wrong.

austinjmorlan, 2017-09-25:
All of the modules must be connected to the Control CAN bus (your computer will not act as a Control CAN bus), meaning that a twisted wire pair must connect from each module's CAN terminal to the next terminal in a daisy chain fashion.

So one of the CAN Gateway's CAN shields must be connected to the car's OBD bus. The second shield (the Control CAN shield) must then have a twisted wire pair running to the CAN terminal of the first of the modules. Then from that terminal another twisted wire pair must run to the second module's CAN terminal. And again from that terminal to the third module's CAN terminal. That module's CAN terminal should then have another twisted pair running back to the CAN Gateway to complete the circuit.

From the Control CAN shield of the gateway you can then run a final twisted wire pair terminated with a 120ohm resistor and a DB9 connector that you can connect your laptop to.

bobjohnson2040, 2017-10-19:
@austinjmorlan Why did you mention that the first and third module should BOTH be connected to the CAN gateway "to complete the circuit"? The CAN wiring should be a line, not a loop.

CAN Gateway --> Module 1 --> Module 2 --> Module 3 --> 120ohm terminated DB9 connector

austinjmorlan, 2017-10-19:
@bobjohnson2040

That's correct, I meant to say that the final module should end in a terminated DB9 connector.

austinjmorlan, 2017-10-30:
@ramanathanrm95 Did my response resolve your issue?

austinjmorlan, 2017-10-31:
@ramanathanrm95 You could attempt to connect to a single module directly (e.g., throttle) from your laptop and see if you're able to communicate with just that one. If so, then there is something wrong with your wiring when you connect multiple.

Run the DB9 connector from one of the module's CAN terminals and connect your Kvaser with a 120ohm terminator to it. Then run joystick commander and attempt to enable.

ramanathanrm95, 2017-10-31:
Will try your suggestions and let you know.
Thanks for the advice. I really appreciate it.

On Tue, Oct 31, 2017 at 11:44 AM, Austin J. Morlan <notifications@github.com
> wrote:

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

Closed 2018-03-12.

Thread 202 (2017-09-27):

Steering error when disconnect power

rg4444, 2017-09-27:
I got the error messages from car - yellow steering wheel and skid control icons in following conditions:
1. The OSCC is off the power, start engine (no errors), switch power - error lights goes on;
2. The engine is off, OSCC is on, switching on engine - no errors, enable controls etc;
3. When controls are enabled touching any - steer brake or accel disables control and steering fallback to normal mode without car errors;
4. When controls are enabled, switching off OSCC power disables controls and switches on steering error light - so steering is in emergency state - no actuation.
Any clues about reasons?
Any relations to this?: I use OBD cable with power switch - if the switch is ON  - whole OSCC is getting power from OBD2 connnector, so emergency switch doesn't operate. If switch is off I got more frequent car error messages.
And after 3+ trials car going to locked mode - so need to connect VCI and erase code to restore power steering.

austinjmorlan, 2017-09-27:
That is expected behavior with the current hardware. OSCC must be powered before the vehicle is turned on. When the OSCC steering module is not powered, it is unable to pass the signal from the steering wheel to the EPAS causing the vehicle to think something is wrong. When the OSCC steering module is powered, it is able to pass the signal through and the vehicle detects nothing is wrong.

Closed 2017-09-27.

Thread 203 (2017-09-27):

Diagramm of tube ports [ PFL PRR PFR PRL PMC1 PMC2 ] for Toyota Prius ABS pump 44510-47050

rg4444, 2017-09-27:
Diagram of Prius ABS tube port location could help installation and prevent installation errors of brake actuator.

rg4444, 2017-09-28:
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
After research this is our educated guess. Pls confirm

jweatherson, 2017-09-29:
[Brake Line Routing.pdf](https://github.com/PolySync/oscc/files/1345193/Brake.Line.Routing.pdf)

Hi there, I assembled this rough schematic to describe the routing of the brake hoses.  Hope this helps.

James

Closed 2017-10-01.

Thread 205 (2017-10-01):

Brake pump motor doesn't switch off, overheat

rg4444, 2017-10-01:
Using actuator board 1.2.0 after initialization and pressure creation pump motor doesn't switch off.
Here is the test video: https://www.youtube.com/watch?v=tR9DBHNbcTs No errors seen on serial monitoring port. All property tests passed.
Secondary problem is un-releasing brake pressure after brake control value is set to 0.

LucasBuckland, 2017-10-04:
Hello, this sounds like you have over-pressured your accumulator. This will cause the pump to keep pumping as the pressure reading is incorrect. Please see issue #131. Which pump power connection are you using? To release the pressure in your accumulator you will need to manually actuate the release valves without the pump pumping.

rg4444, 2017-10-04:
We use 2 wire sets. In one we use both, in one only BM1. Symptoms are the same.
According this Toyota diagram BM1 and BM2 is simply hard connected inside module.
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
How "manually actuate without pump" should be done?
How it is possible to check the pressure readings from pump?

LucasBuckland, 2017-10-19:
BM1 and BM2 are definitely separate from a functional standpoint. Using BM1 significantly increases the longevity of the motor. I'm not sure where that diagram came from but it's different from what I've seen.
There are a couple utilities that are useful; included in the Brake firmware folder. One is the "release_pressure" utility which should be useful in your situation. I highly recommend caution when using any of the utilities; having a full knowledge of the system and being careful to re-flash normal firmware when you are done is essential.

austinjmorlan, 2017-10-30:
@rg4444, did @LucasBuckland resolve your issue?

rg4444, 2017-10-30:
We haven't try yet. Will do after a week and put an update

rg4444, 2017-11-10:
We are using BM1 (pink) wire. The problem isn't stable. One day pump is switching off, one not with the same joystick driver and firmware. Cause is still unclear.

rebpdx, 2018-01-22:
@rg4444 Is the oscc git describe you have compiled for joystick commander with the same as the firmware you flashed on to the brake board? When the pump is staying on does it reach and maintain a pressure?

rg4444, 2018-03-09:
I have narrowed down the cause. Is seams there is pressure inside the system.
The braking system get back to normal operations when pressure lowering after system standby or Utility firmware "release-brake-pressure" is used.
If you have wrote special pressure release utility - there was a reason for it.
Could you elaborate?
What causing pressure problem and how to resolve it without reflashing Arduino time to time?

rg4444, 2018-03-09:
Yes - we are testing and have built latest joystick software together with latest OSCC

rg4444, 2018-03-09:
Started new thread on https://github.com/PolySync/oscc/issues/265

Closed 2018-03-09.

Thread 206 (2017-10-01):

Throttle control problem - no full acceleration

rg4444, 2017-10-01:
On Kia Soul diesel version acceleration control while standing still is working correctly - joystick change value from 0 to 1 and rpm reaches maximum, however while in drive acceleration is week even value is 1. Rpms are not exceeding 2000. Any workaround?

k-cleary, 2017-10-16:
Hey, @rg4444
Which version of the firmware are you using? If you have upgraded to v1.0.0 or greater, you will also need to update your version of joystick commander.
The throttle spoofing should work the same whether the car is in park or in drive.
You may want to check if [stability control](http://www.kisouman.com/electronic_stability_control_esc_-669.html) is enabled. If it is enabled, it might be limiting acceleration.

austinjmorlan, 2017-10-30:
Did @k-cleary resolve your issue?

rg4444, 2017-11-07:
We got the latest version of boards, firmware and joystick commander.
The voltage
Disabled: 0.67.  3.79  Enabled:   0.79  1.37
Disabled: 0.33.  1.79  Enabled:  0.39   0.68
The stability control is disabled
Problem remains

austinjmorlan, 2017-11-09:
Are there any warning lights no the dash?

rg4444, 2017-11-09:
If you mean car's diagnostic error lights - no, there are no any malfunction indicator lights. And there is no reason for that - when OSCC in enabled - voltage values are in expected range - simply performing only as half way pressed accelerator pedal.

austinjmorlan, 2017-11-09:
Am I correct in understanding that you're using the diesel version of the Kia Soul? We haven't tested the diesel version here, so it's possible that the voltage ranges we supply are not valid for your car.

With the car on but not running, and OSCC powered but disabled, you can take a digital multimeter and measure the voltages on the throttle board's "SIG IN A" and "SIG IN B" terminal connections. Measure both with the accelerator pedal not depressed at all, make note of the voltages, and then measure them again with the throttle pedal fully depressed. Compare those voltages to the [ones we've supplied](https://github.com/PolySync/oscc/blob/v1.1.1/api/include/vehicles/kia_soul_petrol.h) (`STEERING_SPOOF_LOW_SIGNAL_VOLTAGE_MIN`,`STEERING_SPOOF_LOW_SIGNAL_VOLTAGE_MAX`,`STEERING_SPOOF_HIGH_SIGNAL_VOLTAGE_MIN`,`STEERING_SPOOF_HIGH_SIGNAL_VOLTAGE_MAX`

rg4444, 2017-11-09:
Yes, it is diesel version. Will make measurements tomorrow and write an update.

rg4444, 2017-11-14:
With the car on but not running, and OSCC powered but disabled, voltages on the throttle board's are:
"SIG IN A" 0.56 to 3.67 V (default 0.7 - 4.1 V)
"SIG IN B" 0.23 to 1.70 V  (default 0.3 - 2 V)
But output is still almost half less.

cotos, 2018-01-22:
Hi @rg4444,

Please run the following test

* Put car in park
* start car
* start JoystickCommander
* `candump -l can0`
* throttle to max
* throttle to min
* kill candump

repeat test with car in drive.

Attach logfiles

rg4444, 2018-03-09:
This is resolved by compiling/updating throttle firmware. By some reason firmware compiled from source before August 2017 got the wrong voltage - only half of required value.

Closed 2018-03-09.

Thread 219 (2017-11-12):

OSCC Configuration parameters  - Adding config for new Car

rg4444, 2017-11-12:
Here is example file of vehicle parameter configuration : https://github.com/PolySync/oscc/blob/v1.1.1/api/include/vehicles/kia_soul_petrol.h
In order to add new vehicle and configure parameters listed below we need more detailed descriptions about values, MIN MAX values and how values might influence the whole system.

Any chances to get descriptions/instructions?

/////BRAKE MODULE Configuration Values////

 * @brief Minimum allowable brake value.
#define MINIMUM_BRAKE_COMMAND ( 0 )

 * @brief Maximum allowable brake value.
#define MAXIMUM_BRAKE_COMMAND ( 52428 )

 * @brief Calculation to convert a brake position to a pedal position.
#define BRAKE_POSITION_TO_PEDAL( position ) ( (position) )

 * @brief Calculation to convert a brake pressure to a pedal position.
#define BRAKE_PRESSURE_TO_PEDAL( pressure ) ( (pressure) )

 * @brief Minimum accumulator presure. [decibars]
#define BRAKE_ACCUMULATOR_PRESSURE_MIN_IN_DECIBARS ( 777.6 )

 * @brief Maximum accumulator pressure. [decibars]
#define BRAKE_ACCUMULATOR_PRESSURE_MAX_IN_DECIBARS ( 878.0 )

 * @brief Value of brake pressure that indicates operator override. [decibars]
#define BRAKE_OVERRIDE_PEDAL_THRESHOLD_IN_DECIBARS ( 43.2 )

 * @brief Brake pressure threshold for when to enable the brake light.
#define BRAKE_LIGHT_PRESSURE_THRESHOLD_IN_DECIBARS ( 20.0 )

 * @brief Minimum possible pressure of brake system. [decibars]
#define BRAKE_PRESSURE_MIN_IN_DECIBARS ( 12.0 )

 * @brief Maximum possible pressure of brake system. [decibars]
#define BRAKE_PRESSURE_MAX_IN_DECIBARS ( 878.3 )

 * @brief Minimum possible value expected to be read from the brake pressure sensors when the pressure check pins (PCK1/PCK2) are asserted.
#define BRAKE_PRESSURE_SENSOR_CHECK_VALUE_MIN ( 665 )

 * @brief Maximum possible value expected to be read from the brake pressure sensors when the pressure check pins (PCK1/PCK2) are asserted.
 #define BRAKE_PRESSURE_SENSOR_CHECK_VALUE_MAX ( 680 )

 * @brief Proportional gain of the PID controller.
#define BRAKE_PID_PROPORTIONAL_GAIN ( 0.65 )

 * @brief Integral gain of the PID controller.
#define BRAKE_PID_INTEGRAL_GAIN ( 1.75 )

 * @brief Derivative gain of the PID controller.
#define BRAKE_PID_DERIVATIVE_GAIN ( 0.000 )

 * @brief Windup guard of the PID controller.
#define BRAKE_PID_WINDUP_GUARD ( 30 )

 * @brief Minimum output value of PID to be within a valid pressure range.
#define BRAKE_PID_OUTPUT_MIN ( -10.0 )

 * @brief Maximum output value of PID to be within a valid pressure range.
#define BRAKE_PID_OUTPUT_MAX ( 10.0 )

 * @brief Minimum clamped PID value of the actuation solenoid.
#define BRAKE_PID_ACCUMULATOR_SOLENOID_CLAMPED_MIN ( 10.0 )

 * @brief Maximum clamped PID value of the actuation solenoid.
#define BRAKE_PID_ACCUMULATOR_SOLENOID_CLAMPED_MAX ( 110.0 )

 * @brief Minimum clamped PID value of the release solenoid.
#define BRAKE_PID_RELEASE_SOLENOID_CLAMPED_MIN ( 0.0 )

 * @brief Maximum clamped PID value of the release solenoid.
#define BRAKE_PID_RELEASE_SOLENOID_CLAMPED_MAX ( 60.0 )

 * @brief Minimum duty cycle that begins to actuate the actuation solenoid 3.921 KHz PWM frequency
#define BRAKE_ACCUMULATOR_SOLENOID_DUTY_CYCLE_MIN ( 80.0 )

 * @brief Maximum duty cycle where actuation solenoid has reached its stop 3.921 KHz PWM frequency
#define BRAKE_ACCUMULATOR_SOLENOID_DUTY_CYCLE_MAX ( 105.0 )

 * @brief Minimum duty cycle that begins to actuate the release solenoid.3.921 KHz PWM frequency
#define BRAKE_RELEASE_SOLENOID_DUTY_CYCLE_MIN ( 65.0 )

 * @brief Maximum duty cycle where release solenoid has reached its stop 3.921 KHz PWM frequency
#define BRAKE_RELEASE_SOLENOID_DUTY_CYCLE_MAX ( 100.0 )

///// STEERING MODULE configuration values

 * @brief Minimum allowable torque value.
#define MINIMUM_TORQUE_COMMAND ( -12.8 )

 * @brief Maximum allowable torque value.
#define MAXIMUM_TORQUE_COMMAND ( 12.7 )

 * @brief Minimum allowable steering DAC output. [volts]
#define STEERING_SPOOF_LOW_SIGNAL_VOLTAGE_MIN ( 0.80 )

 * @brief Maximum allowable steering DAC output. [volts]
#define STEERING_SPOOF_LOW_SIGNAL_VOLTAGE_MAX ( 4.10 )

 * @brief Minimum allowable steering DAC output. [volts]
#define STEERING_SPOOF_HIGH_SIGNAL_VOLTAGE_MIN ( 0.90 )

 * @brief Maximum allowable steering DAC output. [volts]
#define STEERING_SPOOF_HIGH_SIGNAL_VOLTAGE_MAX ( 4.20 )

* @brief Minimum allowed value for the low spoof signal value. [steps]
 * Equal to \ref STEERING_SPOOF_LOW_SIGNAL_VOLTAGE_MIN * \ref STEPS_PER_VOLT.
#define STEERING_SPOOF_LOW_SIGNAL_RANGE_MIN ( 656 )

 * @brief Minimum allowed value for the low spoof signal value. [steps]
 * Equal to \ref STEERING_SPOOF_LOW_SIGNAL_VOLTAGE_MAX * \ref STEPS_PER_VOLT.
#define STEERING_SPOOF_LOW_SIGNAL_RANGE_MAX ( 3358 )

 * @brief Minimum allowed value for the low spoof signal value. [steps]
  * Equal to \ref STEERING_SPOOF_HIGH_SIGNAL_VOLTAGE_MIN * \ref STEPS_PER_VOLT.
#define STEERING_SPOOF_HIGH_SIGNAL_RANGE_MIN ( 738 )

 * @brief Minimum allowed value for the low spoof signal value. [steps]
 * Equal to \ref STEERING_SPOOF_HIGH_SIGNAL_VOLTAGE_MAX * \ref STEPS_PER_VOLT.
#define STEERING_SPOOF_HIGH_SIGNAL_RANGE_MAX ( 3440 )

 * @brief Scalar value for the low spoof signal taken from a calibration curve.
#define TORQUE_SPOOF_LOW_SIGNAL_CALIBRATION_CURVE_SCALE ( 0.135 )

 * @brief Offset value for the low spoof signal taken from a calibration curve.
#define TORQUE_SPOOF_LOW_SIGNAL_CALIBRATION_CURVE_OFFSET ( 2.39 )

 * @brief Scalar value for the high spoof signal taken from a calibration curve.
#define TORQUE_SPOOF_HIGH_SIGNAL_CALIBRATION_CURVE_SCALE ( -0.145 )

 * @brief Offset value for the high spoof signal taken from a calibration curve.
#define TORQUE_SPOOF_HIGH_SIGNAL_CALIBRATION_CURVE_OFFSET ( 2.42 )

 * @brief Value of torque sensor difference that indicates likely operator override.
#define TORQUE_DIFFERENCE_OVERRIDE_THRESHOLD ( 1600 )

// THROTTLE MODULE configuration parameters

 * @brief Minimum allowable throttle value.
#define MINIMUM_THROTTLE_COMMAND ( 0.0 )

 * @brief Maximum allowable throttle value.
#define MAXIMUM_THROTTLE_COMMAND ( 1.0 )

 * @brief Minimum allowed voltage for the low spoof signal voltage. [volts]
#define THROTTLE_SPOOF_LOW_SIGNAL_VOLTAGE_MIN ( 0.30 )

 * @brief Maximum allowed voltage for the low spoof signal voltage. [volts]
#define THROTTLE_SPOOF_LOW_SIGNAL_VOLTAGE_MAX ( 2.00 )

 * @brief Minimum allowed voltage for the high spoof signal voltage. [volts]
#define THROTTLE_SPOOF_HIGH_SIGNAL_VOLTAGE_MIN ( 0.70 )

 * @brief Maximum allowed voltage for the high spoof signal voltage. [volts]
#define THROTTLE_SPOOF_HIGH_SIGNAL_VOLTAGE_MAX ( 4.10 )

 * @brief Minimum allowed value for the low spoof signal value. [steps]
 * Equal to \ref THROTTLE_SPOOF_LOW_SIGNAL_VOLTAGE_MIN * \ref STEPS_PER_VOLT.
 #define THROTTLE_SPOOF_LOW_SIGNAL_RANGE_MIN ( 245 )

 * @brief Minimum allowed value for the low spoof signal value. [steps]
 * Equal to \ref THROTTLE_SPOOF_LOW_SIGNAL_VOLTAGE_MAX * \ref STEPS_PER_VOLT.
#define THROTTLE_SPOOF_LOW_SIGNAL_RANGE_MAX ( 1638 )

 * @brief Minimum allowed value for the low spoof signal value. [steps]
 * Equal to \ref THROTTLE_SPOOF_HIGH_SIGNAL_VOLTAGE_MIN * \ref STEPS_PER_VOLT.
#define THROTTLE_SPOOF_HIGH_SIGNAL_RANGE_MIN ( 573 )

 * @brief Minimum allowed value for the low spoof signal value. [steps]
 * Equal to \ref THROTTLE_SPOOF_HIGH_SIGNAL_VOLTAGE_MAX * \ref STEPS_PER_VOLT.
#define THROTTLE_SPOOF_HIGH_SIGNAL_RANGE_MAX ( 3358 )

 * @brief Value of the accelerator position that indicates operator override. [steps]
#define ACCELERATOR_OVERRIDE_THRESHOLD ( 185.0 )

rebpdx, 2018-01-22:
The min and max values are vehicle and module specific to ensure that the limits are within an expected range of either the actuators or the vehicle voltage lines, and the override threshold for determining if the operator is looking to take control or if there is noise in the signal.

In the case of the header you mentioned a lot of these values are for the add on brake module on the petrol vehicle based on brake pressure in that system. I would recommend starting with something like the kia soul ev or throttle since that is usually a differential voltage signal at the pedal. For example the pedal characteristics could be measured where the intended spoofing would occur and operator override threshold could be determine based on noise in the signal comparison to user's input.

Closed 2018-03-12.

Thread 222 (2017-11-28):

Throttle control problem - Unwanted acceleration

Akashbaskaran, 2017-11-28:
For the joystick control of a Kia Soul, A constant voltage(0.36v & 0.72v) is being spoofed onto the blue and green wires (the voltages are values which corresponds to zero acceleration).
An unwanted acceleration is occurring even when the voltages corresponding to zero acceleration is spoofed.
Any idea why this is the case?

snewt, 2018-01-22:
Hey @Akashbaskaran I've seen this behavior when there is a mismatch between the version of OSCC firmware that was uploaded to the modules and the version joystick commander was built against. I'd check that those versions are identical.

Closed 2018-08-22.

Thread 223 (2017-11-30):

Brake lights remain on if OSCC control is disabled with brakes applied

jweatherson, 2017-11-30:
Kia Soul EV- I've found that the brake lights remain on and the brake light switch relay doesn't open if the brakes are applied on the Joystick while simultaneously the disable button is pressed on the Joystick.  Brake pressure is not present in this state.  Only the lights remain on.

rebpdx, 2018-02-21:
Issue was resolved in PR #248 and included in release [v1.2.0](https://github.com/PolySync/oscc/releases/tag/v1.2.0).

Closed 2018-02-21.

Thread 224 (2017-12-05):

resetting faults

billtyler, 2017-12-05:
I see there is a write up on how to reset faults.  What device or software can be used for this?  I have a kvaser leaf, are you aware of software which can do it?  Or are you using some other device?
I had a hard fault in the steering and had to take it to the dealership to reset it.  Now I have a fault in the throttle module.
thanks

snewt, 2018-01-22:
Hey @billtyler there are a couple options for resetting faults like those. One that seems to be generally capable is the Launch Creader 8001, another is a higher priced KDS tool kit available through GIT America, Inc.

Closed 2018-01-22.

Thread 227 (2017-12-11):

Board Files BOM

ahawcker, 2017-12-11:
In the bill of materials of the boards the column "populate" is empty for some parts. I think that all parts which are not labeled with "dnp" should be populate but i didn't know exactly. Can anybody help?

snewt, 2018-01-22:
Hey there @ahawcker , are you exporting the BOM from a `.sch` file with eagle? I'd like to be on the same page of the same document.

ahawcker, 2018-01-22:
Hi, exactly i'm exporting the BOM from the .sch file with eagle. For example the sensor_interface_V1_1_0.sch, what is with the pin strips (Arduino JP) or the connection terminals (Phoenix_4_45)? I think the most of the parts which have no entry at the populate column should populate. Am I right?

snewt, 2018-01-23:
@ahawcker the BOM associated with each board was not intended to be exported from the schematic so there's no guarantee that what eagle produces from the `.sch` files will be sensical. We recognize that documentation is a valuable resource  and are working on making something available.

snewt, 2018-02-06:
Hey @ahawcker , a BOM for each board was added to the `devel` branch. For example, the BOM for gateway lives here `https://github.com/PolySync/oscc/tree/devel/hardware/boards/gateway`. They are comma delimited CSV files that can be imported into spreadsheet software like Excel or LibreOffice Calc.

Closed 2018-02-06.

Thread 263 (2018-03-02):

Definition of Pins in \brake\include\globals.h

rg4444, 2018-03-02:
There are configuration of Pins like " #define PIN_ACCUMULATOR_PUMP_MOTOR_CHECK ( 8 )"
What is reference for pin numbers?
What could be reason to change the values of pins?

adrienthebo, 2018-03-02:
The pin definitions are based on the actuator control module (https://github.com/PolySync/oscc/blob/master/hardware/boards/actuator_control/actuator_control_1.2.0.pdf). The only motivation I can think of for changing these pin definitions is if you're designing your own brake actuator PCB.

adrienthebo, 2018-03-02:
Since this issue appears to have been addressed I've closed this issue, if you have additional questions please reopen this issue and we can continue this discussion.

Closed 2018-03-02.

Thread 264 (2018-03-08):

AVRDUDE read and write firmware to backup and manage firmware versions on Arduinos

rg4444, 2018-03-08:
There is handy tool call `avrdude` to read and write firmware to Arduino's.
Here are example codes:
Read:
`sudo avrdude -patmega328p -carduino -P/dev/ttyACM0 -b115200 -Uflash:r:/OSCC_Firmware/Read/firmware-throttle.hex:i`
`sudo avrdude -patmega2560 -cstk500v2 -P/dev/ttyACM0 -b115200 -Uflash:r:/OSCC_Firmware/Read/firmware-braking.hex:i`
Write:
`sudo avrdude -patmega328p -carduino -P/dev/ttyACM0 -b115200 -D -V -Uflash:w:/OSCC_Firmware/Write/throttle.hex:i -Ueeprom:w:/OSCC_Firmwares/Write/throttle.eep:i`
However the size of .hex file sent to controller is smaller than downloaded.
What could be cause? Or what are the correct read and write commands to maintain correct structure of firmware in hex file?

shnewto, 2018-03-09:
Hi @rg4444
We rely on some default configuration to upload firmware to the Arduinos using avrdude. That write command for our system is a bit different from the one you've referenced.
```bash
avrdude \
-C/usr/share/arduino/hardware/tools/avrdude.conf \
-patmega328p \
-carduino \
-b115200 \
-P/dev/ttyACM0 \
-D \
-V \
-Uflash:w:OSCC_firmware/Write/throttle.hex \
-Ueeprom:w:OSCC_firmware/Write/throttle.eep:i
```

rg4444, 2018-03-09:
Thank you!
But how about read it back?

PML-Trey, 2018-03-09:
Change the :w: to :r: and set the filename you want it to write to.

Trey

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

rg4444, 2018-03-09:
I did it.
But I concerned about different size of hex files.
If uploaded files are 52,8 and 52,4 kB for throttle/steering, then downloaded is constantly 77,8 kB.

shnewto, 2018-03-09:
Hi @rg4444 ,
I don't have a ready answer about the size discrepancy you're reporting. I may be able to investigate further if you can share the output of the command `avr-size file.hex` for both the uploaded and downloaded files.

rg4444, 2018-03-09:
[read_write_examples.tar.gz](https://github.com/PolySync/oscc/files/1798699/read_write_examples.tar.gz)
Here are 3 different firmware writes and reads.
write
`sudo avrdude -patmega328p -carduino -P/dev/ttyACM0 -b115200 -D -V -Uflash:w:/OSCC_Firmwares/public_examples/can-gateway.hex -Ueeprom:w:/OSCC_Firmwares/public_examples/can-gateway.eep:i -C/usr/share/arduino/hardware/tools/avrdude.conf`

read
`sudo avrdude -patmega328p -carduino -P/dev/ttyACM0 -b115200 -D -V -Uflash:r:/OSCC_Firmwares/public_examples/can-gateway_read.hex:i -C/usr/share/arduino/hardware/tools/avrdude.conf`
please mind missing :i in read command. Without it script through out error

PML-Trey, 2018-03-09:
The firmware images you're programming will only contain the memory needed
for the image while reading flash will read the entire flash.  This seems
consistent with the file sizes you're seeing.

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

Closed 2018-03-10.

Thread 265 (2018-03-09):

Brake pressure release problem - overpressuring - on KIA Soul Petrol

rg4444, 2018-03-09:
After continuously (more than 10 min) excessive braking, ABS unit's  internal brake pressure is increasing, pump motor doesn't switch off, overheat.
Only solution until now is to run firmware : https://github.com/PolySync/oscc/blob/master/firmware/brake/kia_soul_petrol/utils/release_pressure/src/release_pressure.ino
What is the cause for this behavior? Any fixes?

adrienthebo, 2018-03-09:
Hmm, this seems like a worrying issue. I'm not sure that I fully understand everything that's going on, especially since we haven't encountered issues with the ABS unit overheating during testing. In order to help you out I'll need some clarification about some of the details.

  1. What do you define as excessive braking? What brake position were you commanding during this testing? Is the brake pressure applied outside of the range of normal pressures that the vehicle would encounter during an emergency situation?
  2. Was the vehicle in motion and you were testing braking, or were you continuously applying braking as a stress test?
  3. Can you provide the code that caused this behavior?
  4. You mention the ABS unit - are you referring to the electric brake actuator that's installed in series with the standard Kia Soul brake actuator, or is there another stock vehicle system that's overheating?

In addition we have a standard template for filing issues with fields, filling that out would help us get to the bottom of this issue more quickly. Could you fill it out?

### Expected behavior
What should be happening?

### Actual behavior
What behavior are you seeing?

### Steps to reproduce
How can we make it happen too?

### Version info
-  What's the output of running `git describe --tags` in your OSCC directory?
- Is this the same version flashed onto the hardware?

### Hardware info
Are you using a custom board or something received from us?

rg4444, 2018-03-09:
See comments below.
But most important is answer to question for need of special utility for pressure relief.

What do you define as excessive braking?   - Accelerate up to 15mph then stop. More than 20 times in 2 minutes.
What brake position were you commanding during this testing?  -- Joystick control.
Is the brake pressure applied outside of the range of normal pressures that the vehicle would encounter during an emergency situation? --Not sure. Mild braking at low speeds.
Was the vehicle in motion and you were testing braking, or were you continuously applying braking as a stress test? --Vehicle is in the motion.
Can you provide the code that caused this behavior? -- Latest version of firmware, compiled for KIA Petrol + debug flag.
You mention the ABS unit - are you referring to the electric brake actuator that's installed in series with the standard Kia Soul brake actuator, or is there another stock vehicle system that's overheating? --I am referring to Toyota ABS module.

Expected behavior.  -- Normal braking behavior
What should be happening?
Actual behavior
What behavior are you seeing? --
Steps to reproduce  -- Run vehicle for 10 minutes start/stop cycle - to accelerate up to 20 mph and brake by joystick control.
How can we make it happen too? --
Version info
What's the output of running git describe --tags in your OSCC directory?  -- Should be latest version cloned March 8 , 2018
Is this the same version flashed onto the hardware?
Hardware info
Are you using a custom board or something received from us? --Braking board made by/delivered by Polysync August 2017

shnewto, 2018-03-09:
Hi there @rg4444
I'm in favor of getting as much information as possible about this issue so I'll also vote for some of the above template filled out.

As far as potential fixes go however, I can recommend that you try using our brake-monitor. Here's how I suggest it's used.

1. Install the `screen` application. `sudo apt install screen`.
1. Assuming you've already built the firmware and have an `oscc/firmware/build` directory, navigate there. (otherwise, from the `oscc/firmware` directory, run `mkdir build && cd build`)
1. Build the project with debugging on then run the brake-monitor.
```bash
cmake .. -DYOUR_TARET_PLATFORM=ON -DDEBUG=ON ..
make brake-monitor
```
1.  That should launch the brake-monitor. Note that from here, you can run `<ctrl> \` to exit.
1. The following sequence of keys is  `m` `j` `k` `,` is supposed to restore a normal state.
1. If it doesn't, you may have to toggle the master cylinder solenoid with the `i` and `u` keys (until the pedal does not exhibit any "firm resistance".)
1. If step 6 is required, use `m` `j` `k` `,` to get back to a normal state once again before exiting.

For some context, the `m` key is to engage the solenoid, `j` is the command to release pressure in the accumulator, `k` and `,` are to close the actuator and release.

rg4444, 2018-03-09:
Hmm.. Sounds like known problem.
Will try.
Is there a chance to fix it in production environment?

shnewto, 2018-03-09:
By production environment do you mean without the debug flag enabled? If so, the debug flag is only required to use the `brake-monitor` application to restore the brakes to a good state. After that, feel free to restore the firmware to a version without debug flags.

Also, I forgot a couple steps above. The firmware built with the `-DDEBUG=ON` needs to be uploaded to the brake module and when running the `brake-monitor` application you need to be connected to the brake module through USB.

rg4444, 2018-03-09:
I meant production environment when end user could run system flawlessly. Without need to restart, reboot, reconfigure etc

rg4444, 2018-03-20:
I've tried all keyboard buttons in 'screen' terminal window you referred, but seems non of them work. Any pre-requisites for building, launching or pressing keyboard?

shnewto, 2018-03-20:
@rg4444 it looks like I did leave out a step!
While connected to the brake module via USB run the following commands.

```bash
cmake .. -DYOUR_TARET_PLATFORM=ON -DDEBUG=ON ..
make brake-utils-serial-actuator-upload
make brake-monitor
```
Next try the keyboard sequences again.

rg4444, 2018-03-24:
Thank you! Now its working. All solenoids are operating by key strokes. Biggest problem is that pressure debug readings are not implemented on joystick controllable firmware version.

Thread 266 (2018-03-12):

throttle fault issue

billtyler, 2018-03-12:
I have a few feet of wire for the throttle sensor run up to the passenger seat for when I hook up the computer for testing etc.  This has worked without issue for a few months, however in the last week or so it has faulted twice.  I'm currently sitting at a Starbucks waiting for it to reset and allow normal driving again.

Based on the few times I have experienced this I know it will reset after some time, does anyone know how long it takes for this?

Any ideas on making sure it does not trip for simply jostling the wires?

shnewto, 2018-03-12:
Hey there @billtyler ,
I'd recommend picking up a diagnostic tool like the Launch Creader if you're able (https://www.amazon.com/Launch-Creader-Scanner-Functions-Diagnostic/dp/B01N36W561). That should provide more specific context around your faults and hopefully enough information to help you spot the problem that's causing it.

billtyler, 2018-03-13:
I was able to get a get a scanner and reset two of the three codes.  It drives now but there is a code listed as permanent - P2127 Throttle/Pedal Position Sensor / Switch "E" Circuit Low Input.  Are "permanent" code only able to be reset by the Kia device?

rebpdx, 2018-03-15:
I'm not sure about permanent codes and which devices do and do not reset them. I'd recommend making sure there aren't any intermittent connections or any high impedance for the Pedal Position Sensor described by the fault and then try resetting it.

Closed 2018-03-12.

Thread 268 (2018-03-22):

Unequal brake pressure FR and FL wheels on KIA Soul Petrol Toyota ABS

rg4444, 2018-03-22:
We are experiencing unequal brake pressure using joystick commander.
Here is test video: [https://www.youtube.com/watch?v=1pKUC6Q5qEs]
In the same test environment manual brakes are working equally on all 4 wheels.
After entering joystick mode:
- rear wheels are braking equally;
- front wheels in low-to-middle braking forces are working unequally. Difference is more than 50% which is not permitted by regulation. In our case more pressure is applied to front left wheel.
Is there a way how to adjust pressure in firmware settings, as well as monitor software pressure value output in real time?
What was a reason to not include pressure monitor values in debug version of brake board firmware?

cotos, 2018-03-22:
Hi rg4444,

This seems like a mechanical issue to me.
* Verify there is no air in the brake lines going to the front right and left brakes.
* Uneven brake pressure may indicate an issue with the Toyota ABS.

The brake system digram is on this [page](https://github.com/PolySync/oscc/wiki/Hardware-Brake-%28Petrol%29)

We do not have firmware settings to adjust brake pressure for individual brake solenoids.
We do have a "Serial Actuator" utility that will monitor brake pressure on the front right and left brake solenoids.

### Make the “Serial Actuator” utility.
```
$ cd ~/OSCC/firmware && mkdir build && cd build
$ cmake .. -DKIA_SOUL=ON -DDEBUG=ON
$ make
```

### Upload the Serial Actuator utility
Connect the actuator module to a laptop to using a USB A-B cable.
`$ make brake-utils-serial-actuator-upload`

### Monitor the serial output over USB.
`$ make brake-monitor`

Note:  screen must be installed
`$ sudo apt install screen`

### Exit Serial Actuator utility
```
$ <ctrl> a \
$ yes
```

### Measurements we see when running this test:
Test set up for brake-monitor test
Car is off
Power is applied to brake module (if you hear the brake pump during the brake pump verification step power is applied)
Verify you can hear the solenoids activate and deactivate
Press "m" (you should hear the relay engage)
Press "," (you should hear the relay disengage)
Press "j" (you should hear the relay engage)
Press "k" (you should hear the relay disengage)
Test the master cylinder
press the "i" key on the keyboard to close master cylinder solenoid
press the brake pedal
**CAN,0,PACC,12.00,PFL,12.00,PFR,12.00,PMC1,172.70,PMC2,199.10**
press the "u’’ key on the keyboard to close master cylinder solenoid
press the brake pedal
**CAN,0,PACC,12.00,PFL,153.50,PFR,151.10,PMC1,184.70,PMC2,184.70**
Get to a known state Release all the pressure in the accumulator Press “m” “j” Press “k” and “,” to close the actuator and release solenoids You should see something similar to this **CAN,0,PACC,12.00,PFL,12.00,PFR,12.00,PMC1,12.00,PMC2,12.00**
Press the brake You should see
**CAN,0,PACC,12.00,PFL,98.30,PFR,83.90,PMC1,100.70,PMC2,117.50**
Verify brake pump is adding pressure and PACC stays pressurized
Press the ‘p’ key on the keyboard. The accumulator, pumping up pressure, should be audible. The PACC pressure should increase.
After 5 seconds press '['
PACC should be ~800
Wait 20 seconds the value should not decrease by more than 2%
You should see
**CAN,0,PACC,842.30,PFL,12.00,PFR,12.00,PMC1,12.00,PMC2,12.00**
Ensure that the master cylinder solenoid is working properly
press the "i" key on the keyboard to close master cylinder solenoid
press the brake pedal
**CAN,0,PACC,12.00,PFL,12.00,PFR,12.00,PMC1,172.70,PMC2,199.10**
test the proper operation of the “actuator” and “release” solenoids to the wheels.
press "," to ensure that the “release” solenoid is closed
press the ‘j’ key to open the actuator solenoids. (You should hear the solenoid disengage)
You should see
**CAN,0,PACC,866.30,PFL,878.30,PFR,878.30,PMC1,12.00,PMC2,12.00**
Get back to a known state
Press “m” (you should hear the solenoid engage, PACC will go to ~12.00)
PRESS “j” to release all the pressure in the accumulator
Press “k” and “,” to close the actuator and release solenoids
You should see something similar to this
**CAN,0,PACC,12.00,PFL,12.00,PFR,12.00,PMC1,12.00,PMC2,12.00**

rg4444, 2018-03-24:
Great tutorial! Thank you
All solenoids are working as expected - pressure  readings are legit - see chart below
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

rg4444, 2018-03-24:
Is there a way how to get the same pressure readings in ordinary brake firmware? What was a reason to not integrate debug pressure readings in base firmware, so pressure could be monitored in fully operational mode , i.e. joystick controller?
Are there any tools to visualize realtime data from _screen_ - to draw realtime charts?

rg4444, 2018-03-25:
Command descriptions:
'u': Master_cylinder_open - "opened SMCs"
'i': Master_cylinder_close - "closed SMCs"
'j': Set_accumulator_solenoid_duty_cycle( SOLENOID_PWM_ON ) -"opened SLAs"
'k': Set_accumulator_solenoid_duty_cycle( SOLENOID_PWM_OFF ) - "closed SLAs"
'm': Set_release_solenoid_duty_cycle( SOLENOID_PWM_ON ) - "opened SLRs"
',': Set_release_solenoid_duty_cycle( SOLENOID_PWM_OFF ) - "closed SLRs"
'p': Accumulator_turn_pump_on
'[': Accumulator_turn_pump_off
https://raw.githubusercontent.com/wiki/PolySync/oscc/images/brake_module/brake_stock_diagram.png

rg4444, 2018-04-01:
After adding debug code to firmware here are the readings from both: joystick control and manual pedal.
[sdp1.xlsx](https://github.com/PolySync/oscc/files/1866624/sdp1.xlsx)
There is difference between readings from FR and FL sensors. For some unknown reason FR pressure are higher than FL. Also FL seemingly lagging in time - by responding later. Its happening even in manual pedal operation. Any clues?

JesseS95, 2019-10-15:
Hi mate,
I'm testing the brake module for the petrol Kia soul.
I find that the relay 3 is flickering.
Should this relay be flickering on and off (sometimes too fast for the pump to even start)  when the brakes are not applied?

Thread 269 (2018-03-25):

KIA SOUL Petrol brake module solenoid operation sequences and checks

rg4444, 2018-03-25:
What is the logic and sequence of default braking module firmware?

1. Booting up for the first time
Upload of firmware successfully finished. USB wire plugged out, OSCC electricity supply switched off.
OSCC powered up. Joystick controller set to enable mode.
What management module should do and in what sequence?
Like:
---OSCC powered up for first time
1. Check the solenoid state:
Master cylinder_ SMCs - should be open. If close - open up.
Pressure fill solenoids  - SLAs - should be closed. If open - close down
Pressure spill solenoids - SLRs - should be closed. If open - close down
(What happening if solenoids are left in wrong state? I have seen test scenario when ABS unit is powered up with open output brake lines and solenoids are open - so pump is trying to build the pressure, which flowing out from brake lines)
2. Check for PACC pressure - if under 500 - switch on the Accumulator
 pump ('p'). When pressure reach 800 - turn accumulator power off ('[')
----- Enabling control
Close master cylinder SMCs
Waiting for brake command
----- Pressing brake on joystick
Release SLA solenoids accordingly to the braking intensity
----- Releasing  brake on joystick
Close SLA solenoids
Open SLR solenoids to release the pressure.
Close SLR solenoids when pressure released to 12.
-----Disable joystick control
Open Master cylinder's SMCs

Please correct to the right descriptions. Thank you in advance.

rg4444, 2018-04-01:
Summary of findings. Some commands are duplicated, not sure about consequences.
One time on initialization:
`1.	init_arduino
2.	init_communication_interfaces
2.1.	init_serial
2.2.	unit_CAN
3.	init_globals
4.	init_devices
4.1.	    accumulator_init
4.1.1.	     PIN_ACCUMULATOR_PUMP_MOTOR, set as OUTPUT
4.1.2.	    accumulator_turn_pump_off
4.1.2.1.	PIN_ACCUMULATOR_PUMP_MOTOR, Set as LOW = 0V
4.2.	    master_cylinder_init
4.2.1.	    PIN_MASTER_CYLINDER_SOLENOID, set as OUTPUT
4.2.2.	    master_cylinder_open ("opened SMCs")
4.2.2.1.	    PIN_MASTER_CYLINDER_SOLENOID, SOLENOID_PWM_OFF = 0
4.2.2.2.	    DEBUG_PRINT "Master Cylinder Open"
4.3.	    brake_init
4.3.1.	    PIN_ACCUMULATOR_SOLENOID_FRONT_LEFT, LOW = 0V
4.3.2.	    PIN_ACCUMULATOR_SOLENOID_FRONT_RIGHT, LOW = 0V
4.3.3.	    PIN_RELEASE_SOLENOID_FRONT_LEFT, LOW = 0V
4.3.4.	    PIN_RELEASE_SOLENOID_FRONT_RIGHT, LOW = 0V
4.3.5.	    PIN_WHEEL_PRESSURE_CHECK_1, LOW = 0V
4.3.6.	    PIN_WHEEL_PRESSURE_CHECK_2, LOW = 0V
4.3.7.	    set_release_solenoid_duty_cycle SOLENOID_PWM_OFF
4.3.8.	    set_accumulator_solenoid_duty_cycle SOLENOID_PWM_OFF
4.3.9.	    disable_brake_lights
4.3.9.1.	PIN_BRAKE_LIGHT, LOW = 0V
4.3.10.	startup_check ???
4.4.	    accumulator_turn_pump_off
4.4.1.	PIN_ACCUMULATOR_PUMP_MOTOR, Set as LOW = 0V
4.5.	    master_cylinder_open ("opened SMCs")
4.5.1.1.	    PIN_MASTER_CYLINDER_SOLENOID, SOLENOID_PWM_OFF = 0
4.5.1.2.	    DEBUG_PRINT "Master Cylinder Open"
4.6.	    set_release_solenoid_duty_cycle SOLENOID_PWM_OFF
4.7.	    set_accumulator_solenoid_duty_cycle SOLENOID_PWM_OFF
5.	init_communication_interfaces
5.1.	    init_serial
5.2.	    DEBUG_PRINT "init Control CAN - "
5.3.	    Init CAN
6.	start_timers
6.1.	timer1_init( FAULT_CHECK_FREQUENCY_IN_HZ, check_for_faults
6.2.	timer2_init( OSCC_BRAKE_REPORT_PUBLISH_FREQ_IN_HZ, publish_brake_report
7.	DEBUG_PRINT: "init complete"
 

Continuously:
1.	check_for_incoming_message
2.	accumulator_maintain_pressure
2.1.	    float pressure = accumulator_read_pressure( );
2.2.	    if ( pressure <= BRAKE_ACCUMULATOR_PRESSURE_MIN_IN_DECIBARS )
2.3.	    accumulator_turn_pump_on( );
2.3.1.	PIN_ACCUMULATOR_PUMP_MOTOR, HIGH = 5V
2.4.	    else if ( pressure >= BRAKE_ACCUMULATOR_PRESSURE_MAX_IN_DECIBARS )
2.5.	   accumulator_turn_pump_off
2.5.1.	PIN_ACCUMULATOR_PUMP_MOTOR, LOW = 0V
3.	    check_for_operator_override
4.	update_brake
`

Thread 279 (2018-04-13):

Fault callback is never invoked

zolnierczyk, 2018-04-13:
Hi PolySync,

I think that I found bug with fault handling mechanism.

### Expected behavior
OSCC C api fault_report_callback should be invoked where CAN error frame is received.

### Actual behavior
All error frames are ignored.

### Steps to reproduce
For example brake module:
1. Disconnect module from car system but keep CAN connection to oscc part
2. Power it up
3. Send enable command
4. Module send CAN error frames (CAN sniffer show frames)
5. OSCC C api don't receive any faults

### Version info
Source from v1.2.1-niro

### Analyze
SocketCAN is initialized by this code:
```
    struct sigaction sig;
    memset( &sig, 0, sizeof(sig) );
    sigemptyset( &sig.sa_mask );
    sig.sa_flags = SA_RESTART;
    sig.sa_handler = oscc_update_status;
    sigaction( SIGIO, &sig, NULL );

    int sock = socket( PF_CAN, SOCK_RAW, CAN_RAW );

    if ( sock < 0 )
    {
        printf( "Opening CAN socket failed: %s\n", strerror(errno) );
    }
    else
    {
        result = OSCC_OK;
    }
```

But from kernel documentation we can read [kernel doc](https://www.kernel.org/doc/Documentation/networking/can.txt)

> Using CAN_RAW sockets is extensively comparable to the commonly
  known access to CAN character devices. To meet the new possibilities
  provided by the multi user SocketCAN approach, some reasonable
  defaults are set at RAW socket binding time:
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

So current behavior that api don't get any error frames is valid one from kernel driver point of view. I modify code by adding new header include:
```
#include <linux/can/raw.h>
#include <linux/can/error.h>
```
And also after creating socket new option:
```
can_err_mask_t err_mask = ( CAN_ERR_MASK );
setsockopt(sock, SOL_CAN_RAW, CAN_RAW_ERR_FILTER, &err_mask, sizeof(err_mask));
```
And after this modification I can receive fault code and callback is invoked.

rebpdx, 2018-04-14:
Thank you for the information. We're working on reproducing it.

What vehicle are you running?

In the firmware we are not deliberately sending error frames for those fault reports which suggests that the CAN bus is having some difficulty sending messages. Are the error frames the only CAN frames you are seeing?

zolnierczyk, 2018-04-16:
I am working on Kia Niro vehicle but currently I reproduce this bug just by connecting all modules together with power and CAN just on the table without car connected to any board. I am receiving report frames correctly and I can send enable message to boards on which they react. But as you mention those errors came from bus itself.
[Testing without my modification] With one module powered up I got callback called properly. With two modules powered up I got error frames  sometimes without callback called and with three module problem was bigger. The root case of issue I think is sending fault report frame:
```
g_control_can.sendMsgBuf(
        OSCC_FAULT_REPORT_CAN_ID,
        CAN_STANDARD,
        OSCC_FAULT_REPORT_CAN_DLC,
(uint8_t *) &fault_report );
```
All three modules was trying to send fault report frame with the same ID and at the same time which give bus error message. Of course boards are not perfectly synchronized so I am still getting some valid fault frames.

This setup is not representing real life scenario. There is small probability that all boards start to send fault frames so this is not big issue but nevertheless I think it is good idea to create fault frames ID per module not common for every one.

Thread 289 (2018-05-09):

Male/Female connector part numbers for throttle/brake/steering?

frk2, 2018-05-09:
Hey guys,
Not a bug per-se but more a request for information if someone has done this. I'm looking for part numbers for male/female connectors for the throttle/brake position sensor and the steering torque sensor connector. I'm trying to make clean Y connectors for everything to plug OSCC into my car.

The only thing ive been able to find is that the brake connector housing is this one:
https://www.mouser.com/ProductDetail/571-1-967616-1

Does anyone have more information on what housings they used? Or is everyone splicing wires to get this to work?

Also curious if its possible to pay extra to get all these connectors / pigtails shipped from polysync!

Thank you

DavidSosnow, 2018-05-09:
Hi Faraz,

We've done the hard-work of tracking down or building various connectors, designing automotive-grade wiring harnesses (that tie cleanly into the vehicle), and more in our DriveKit product. Unfortunately, we can't sell just the individual parts, but if you're curious to learn more about DriveKit let us know.

https://polysync.io/drivekit/

frk2, 2018-05-09:
@DavidSosnow I fully understand and respect that. Im actually doing this for a opensource project (https://frk2.github.io/opencaret/) and am unable to pay the full amount ($20k) for drivekit at the moment. I'm willing to pay a heavy premium for these connectors if you guys can simply ship me the harness that you guys use with drivekit! Is that doable?

OAkyildiz, 2019-09-20:
@kenkeiter We understand that, but are you also stating that you do not want to disclose what cable harnesses you are using?
(For the interested, I found the male connector for KIA Soul EV brake)

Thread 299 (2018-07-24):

throttle graph in wiki is missing.

asimay, 2018-07-24:
<!--
Thanks for filing an OSCC issue! You're making our ecosystem a better place!

Below are some templates to get you started, filling out any that are relevant
to this issue will help us a lot! Feel free to delete any information or text
that isn't relevant to your issue.
-->

<!-- Questions about purchasing and pricing for OSCC boards or DriveKit?
Shoot an email to drivekit@polysync.io -->

<!--
Technical issue template.

Are you having a technical issue? Fill in the following blocks to help us
tackle it!
-->

### Expected behavior
<!-- What should be happening? -->

### Actual behavior
<!-- What behavior are you seeing? -->
**throttle graph in wiki is missing.**

### Steps to reproduce
<!-- How can we make it happen too? -->
https://github.com/PolySync/oscc/wiki/Hardware-Throttle

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

### Version info
- _What's the output of running `git describe --tags` in your OSCC directory?_
- _Is this the same version flashed onto the hardware?_

### Hardware info
<!-- Are you using a custom board or something received from us? -->

<!--
Feature/changes issue template.

Are you interested in a new feature or a change to something that exists?
Fill in the following blocks to help us understand it!
-->

### Proposed feature or changes
<!-- What would you like to accomplish? -->

### Use case
<!-- How would you like to do it? -->

<!--
Documentation issue template.

Have you found a bug in documentation or wish something was documented that
isn't? Fill in the following blocks to help us help you!
-->

### Documentation expected
<!-- What information would help you? Where would you expect to find it? -->

### Documentation available
<!-- What were you able to find? Was it in the right spot? -->

<!--
Is your issue something that doesn't fit any of the templates above?
Let us know here!
-->

shnewto, 2018-07-24:
Hi @asimay thanks for pointing this out! I've attached included the image here while we work out updating the wiki.
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

shnewto, 2018-07-24:
Image link updated. Thanks again for pointing it out @asimay

Closed 2018-07-24.

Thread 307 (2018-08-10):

Unit Test Issue - avr-g++ error: shared is not supported

TommyBlairesLewis, 2018-08-10:
### Expected behavior
<!-- What should be happening? -->
Pass the Unit Test and the Property Test

### Actual behavior
<!-- What behavior are you seeing? -->
1. I got the sys/timeb.h issue and got it solved by `export` the C library to `/usr/include/`
2. I experienced several errors from `stdio` library and solved by installing `apt-get gcc-avr`
3. Now whenever I try to run `make run-unit-tests`, I always see avr-g++ error: shared is not supported.

### Steps to reproduce
<!-- How can we make it happen too? -->
Install the framework environment for OSCC and purged the arduino library. Following original OSCC steps to run the Unit test and Property test.

shnewto, 2018-08-10:
Hi @TommyBlairesLewis thanks for raising this issue! I'm currently unable to reproduce the behavior your seeing so any more information about your setup would help me investigate further. Minimally the output of `uname -a` would be useful.

When you say "purged the arduino" library, you mean you followed the steps here https://github.com/PolySync/oscc#pre-requisites?

TommyBlairesLewis, 2018-08-13:
Thanks for responding @shnewto @rebpdx

Here's my current build output after installing the `zlib1g-dev`

[  2%] Building CXX object throttle/tests/CMakeFiles/throttle.dir/__/__/common/testing/mocks/Arduino_mock.cpp.obj
[  4%] Building CXX object throttle/tests/CMakeFiles/throttle.dir/__/__/common/testing/mocks/mcp_can_mock.cpp.obj
[  6%] Building CXX object throttle/tests/CMakeFiles/throttle.dir/__/__/common/testing/mocks/DAC_MCP49xx_mock.cpp.obj
[  8%] Linking CXX shared library libthrottle.so
CMakeFiles/throttle.dir/__/src/communications.cpp.obj: In function `publish_throttle_report()':
/home/control-box/oscc/firmware/throttle/src/communications.cpp:45: undefined reference to `MCP_CAN::sendMsgBuf(unsigned long, unsigned char, unsigned char, unsigned char*)'
CMakeFiles/throttle.dir/__/src/communications.cpp.obj: In function `publish_fault_report()':
/home/control-box/oscc/firmware/throttle/src/communications.cpp:64: undefined reference to `MCP_CAN::sendMsgBuf(unsigned long, unsigned char, unsigned char, unsigned char*)'
CMakeFiles/throttle.dir/__/__/common/libs/can/oscc_can.cpp.obj: In function `check_for_rx_frame(MCP_CAN&, can_frame_s*)':
/home/control-box/oscc/firmware/common/libs/can/oscc_can.cpp:39: undefined reference to `MCP_CAN::readMsgBufID(unsigned long*, unsigned char*, unsigned char*)'
/usr/lib/gcc/avr/4.8.2/../../../avr/lib/libc.a(malloc.o): In function `malloc':
/build/buildd/avr-libc-1.8.0/avr/lib/avr2/../../../libc/stdlib/malloc.c:69: undefined reference to `__heap_end'
collect2: error: ld returned 1 exit status
make[3]: *** [throttle/tests/libthrottle.so] Error 1
make[2]: *** [throttle/tests/CMakeFiles/throttle.dir/all] Error 2
make[1]: *** [CMakeFiles/run-unit-tests.dir/rule] Error 2
make: *** [run-unit-tests] Error 2

shnewto, 2018-08-14:
Hi @TommyBlairesLewis, thanks for providing that output. I don't think we've tried building on Ubuntu 14.04 but I'll give it a try myself and see if I can reproduce / resolve what you're seeing.

shnewto, 2018-08-14:
@TommyBlairesLewis an update on my side. I don't think there's an easy way to run our unit tests on Ubuntu 14.04. Aside from the avr issues you're running into, our tests depend on custom cgreen and cucumber-cpp libraries that are built for Ubuntu 16.04. The libraries live here https://github.com/PolySync/oscc/tree/master/firmware/common/testing/framework.

I experimented with what it would look like to build them individually for 14.04 and it's pretty labor intensive. I abandoned ship when it started to require building an older version of boost from source and statically linking it to cucumber-cpp in a custom CMakeLists.txt.

If you are still very interested in running the unit tests on Ubuntu 14.04 I'd recommend raising another issue as a feature request and referencing this conversation / issue number so we can track it.

TommyBlairesLewis, 2018-08-14:
@shnewto

I can move to 16.04 and try it again. I think the reason we do 14.04 because of the ML stuffs dependencies we wrote. Some of them won't work well with 16.04 even 18. However, for testing purpose only, I don't mind to switch 16.04.

Closed 2018-08-21.

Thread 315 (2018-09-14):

Steering control at 0 MPH

TommyBlairesLewis, 2018-09-14:
### Expected behavior
<!-- What should be happening? -->
The steering control should be able to turn fully left and right at 0MPH after the ignition

### Actual behavior
<!-- What behavior are you seeing? -->
The steering is moving but it doesn’t flow full to the right or left 90 degree wise. If the steering gets an extra help, it’d show an error. I guess the release build because DSTEERING was ON.

### Steps to reproduce
<!-- How can we make it happen too? -->
Splice only two wires from MOBIS MDPS Kia Niro. White wire is connected to High and Gray color is connected to low. Jumper the SIG A High and SIGB Low to Input and output
Kia C CAN is disconnected, although it should be connected through OBD but I keep getting C CAN is not connected. This particular issue only runs by the steering torque spoof.

### Version info
- _What's the output of running `git describe --tags` in your OSCC directory?_
- _Is this the same version flashed onto the hardware?_

Yes, the same with the hardware. Latest release 1.0.0, I assume.

### Hardware info
<!-- Are you using a custom board or something received from us? -->
PolySync original OSCC

We created a quick video for better description

https://youtu.be/ogRkbVM3qvg

cotos, 2018-09-14:
With 1.0.0 hardware you want to use the 1.0.0 tag
ref:  https://github.com/PolySync/oscc#versions
```
~/oscc$ git describe --tags
v1.0.0
```
You can adjust the steering speed in `oscc-joystick-commander` by doing the following:
```
#define STEERING_RANGE_PERCENTAGE (0.2)  # increase to 4 or 5 to increase steering speed
```
You can increase the steering responsiveness by adjusting the STEERING_RANGE_PERCENTAGE
We keep it low by default to avoid steering errors.
You may find .36 to be an acceptable value.
ref: https://github.com/PolySync/oscc-joystick-commander/blob/devel/src/commander.c#L31

When testing steering at 0 MPH you may consider making some turn-tables.

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

Best,
Chris

Closed 2018-09-14.

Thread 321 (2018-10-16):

The meaning of the P$1 - P$2 Contacts/Pins on Actuator Control Board?

zxiongunsw, 2018-10-16:
Hello everyone, we are having difficulty in understanding what the P$1 and P$2 pins/contacts are on the Actuator control board. I have included a snapshot with all the eights pints circled in red.

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

Could you let me know how those pins are related to the Brake actuator or any other components in OSCC? Thanks a lot!

cotos, 2018-10-16:
Hi zxiongunsw,

They are mounting holes for the `solenoid banks` heat sinks.

Closed 2018-10-16.

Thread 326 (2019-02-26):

Something about PCB

JesseS95, 2019-02-26:
Hi all,

there are some parts in the BOM but not on the PCB.

sensor_interface : C19

actuator_control: RELAY2 R29 R31 D5

Vehicle_control: R24 R25

What are they used for ?

PML-Trey, 2019-02-26:
sensor_interface : C19
C19 Looks to be an error in the BOM

actuator_control: RELAY2 R29 R31 D5
RELAY2 is the actual relay.  It is socketed and fits in RELAY3.
R29 and R31 are used to seperate the sense nets so they can be named to enable differential routing in EAGLE.
D5 is a diode to protect against back EMF from the solenoid.

Vehicle_control: R24 R25
R24 R25 Look to be an error in the BOM

I suspect the errors are due to earlier versions of the boards having these parts.

JesseS95, 2019-02-28:
Hi Trey, In terms of actuator_control: Where are the position of R29, R31, D5 on the board?

PML-Trey, 2019-02-28:
R29 and R31 are just to the left of CON5 and CON7. D5 is directly behind CON5.

Closed 2019-02-26.

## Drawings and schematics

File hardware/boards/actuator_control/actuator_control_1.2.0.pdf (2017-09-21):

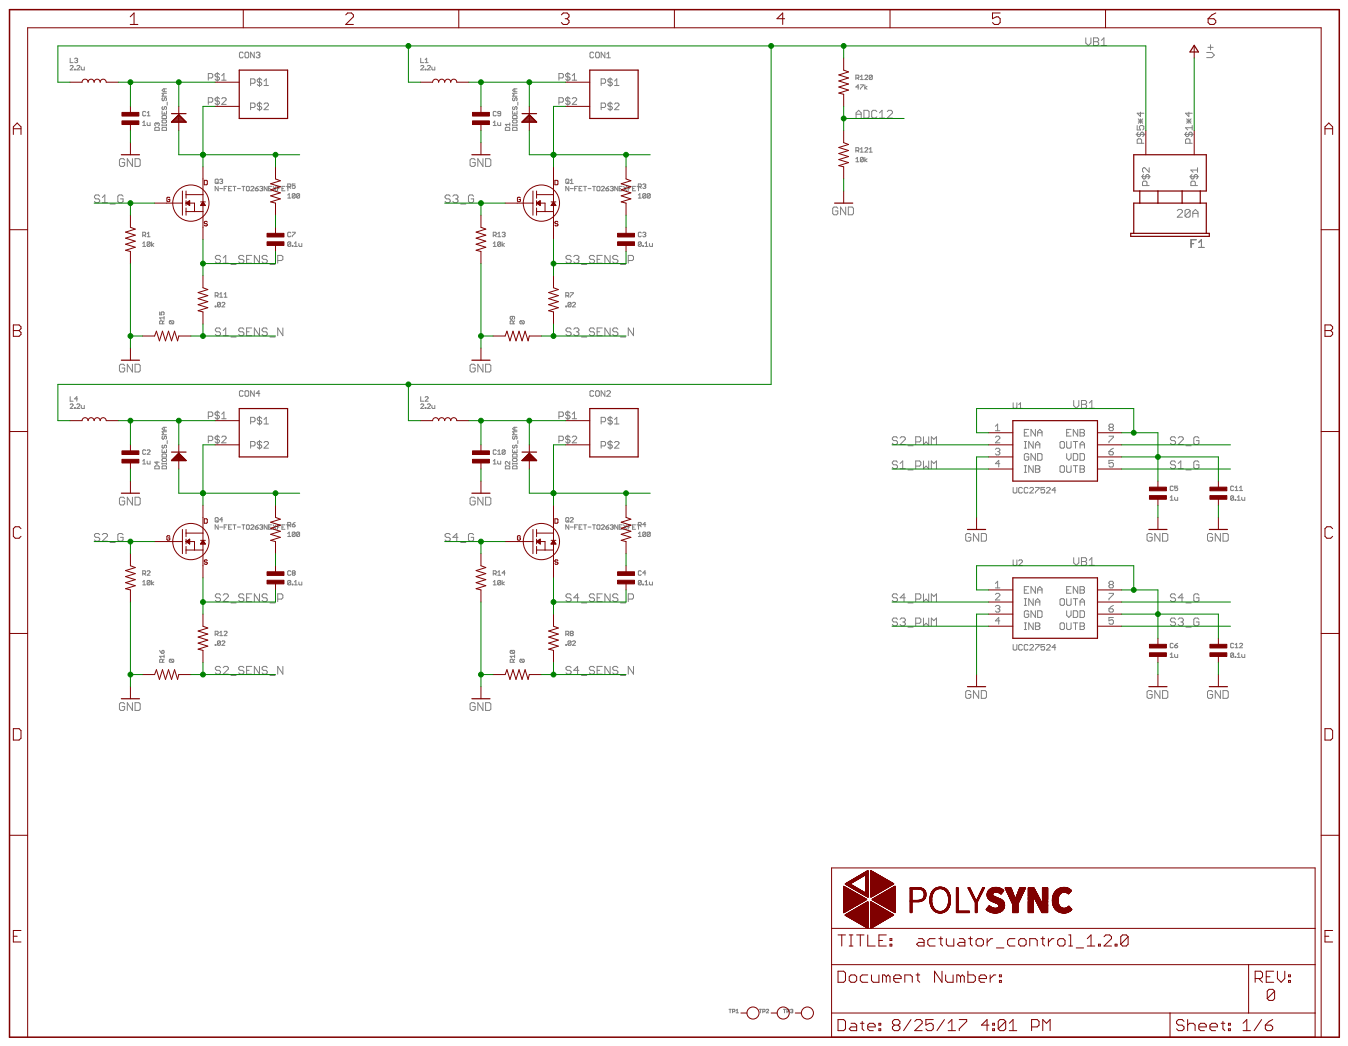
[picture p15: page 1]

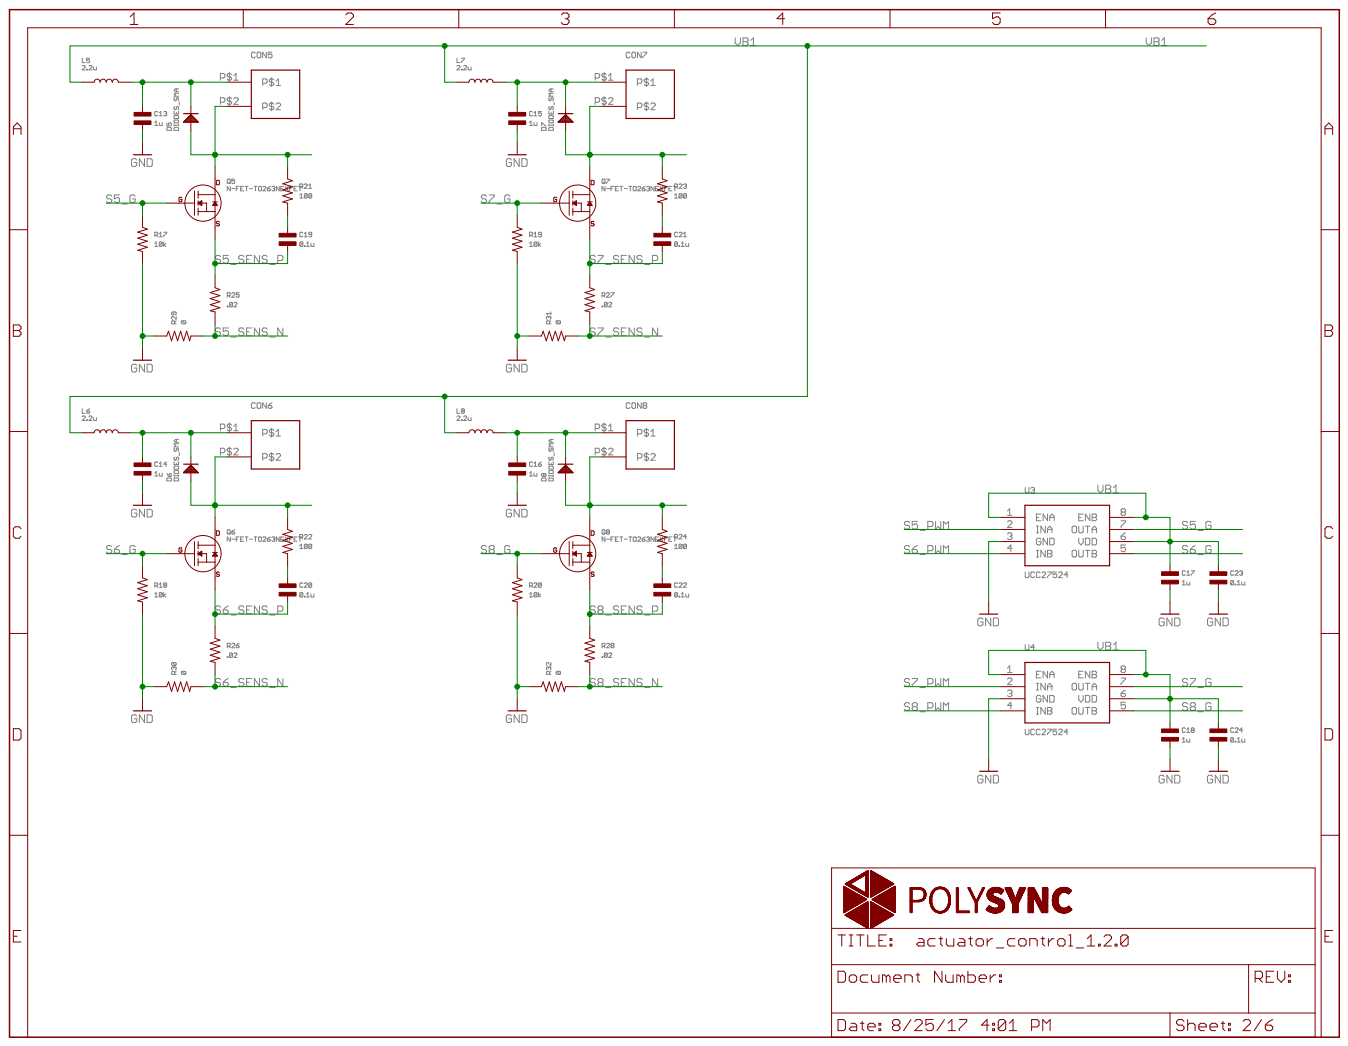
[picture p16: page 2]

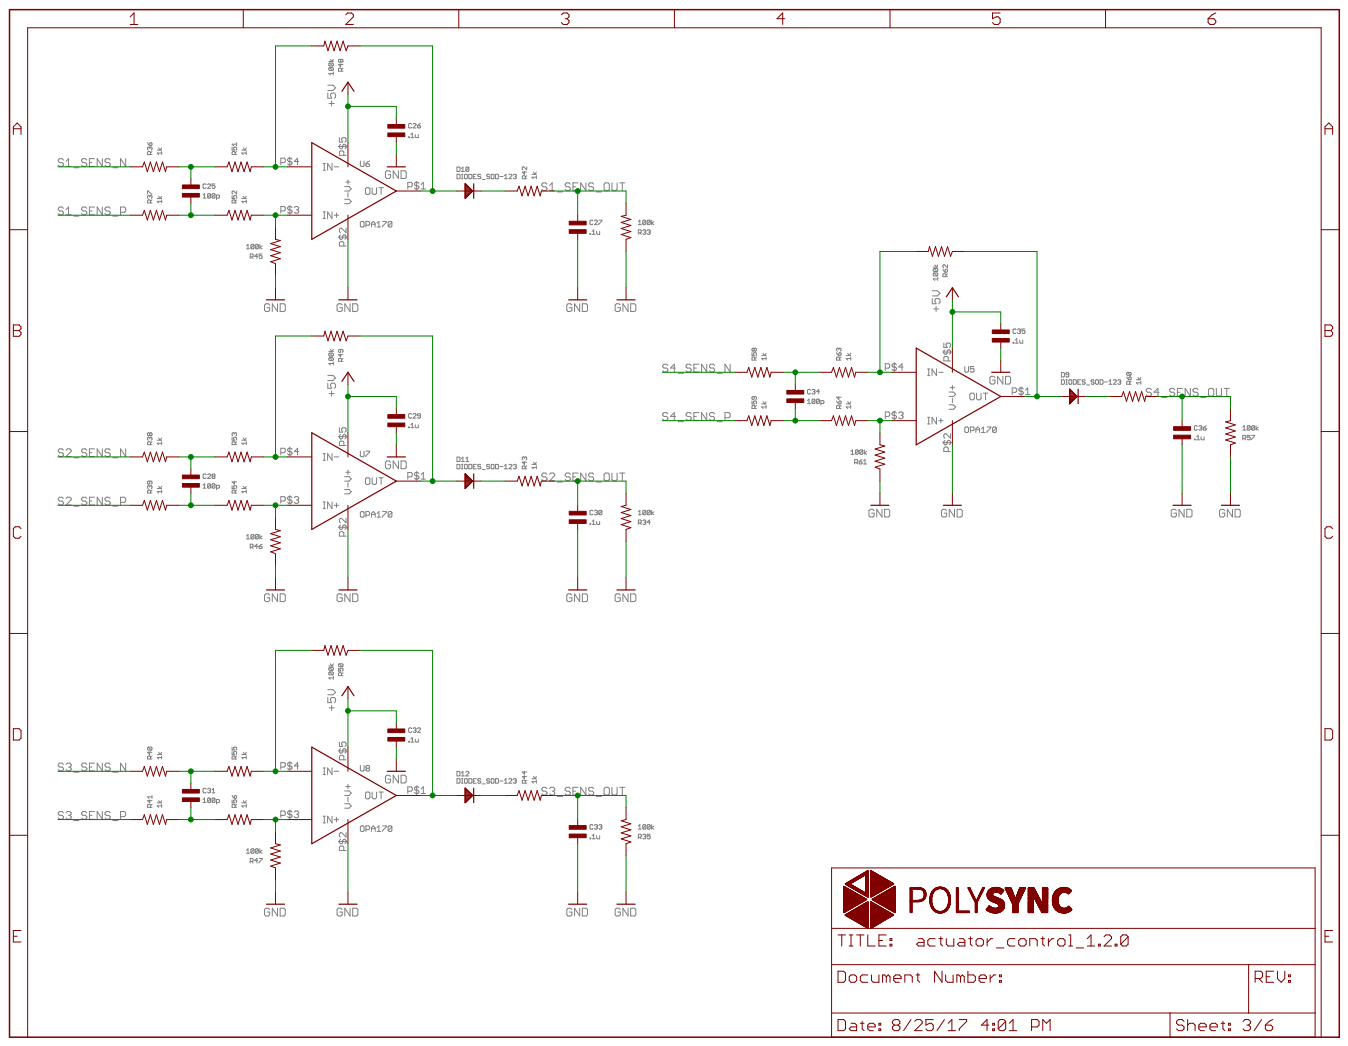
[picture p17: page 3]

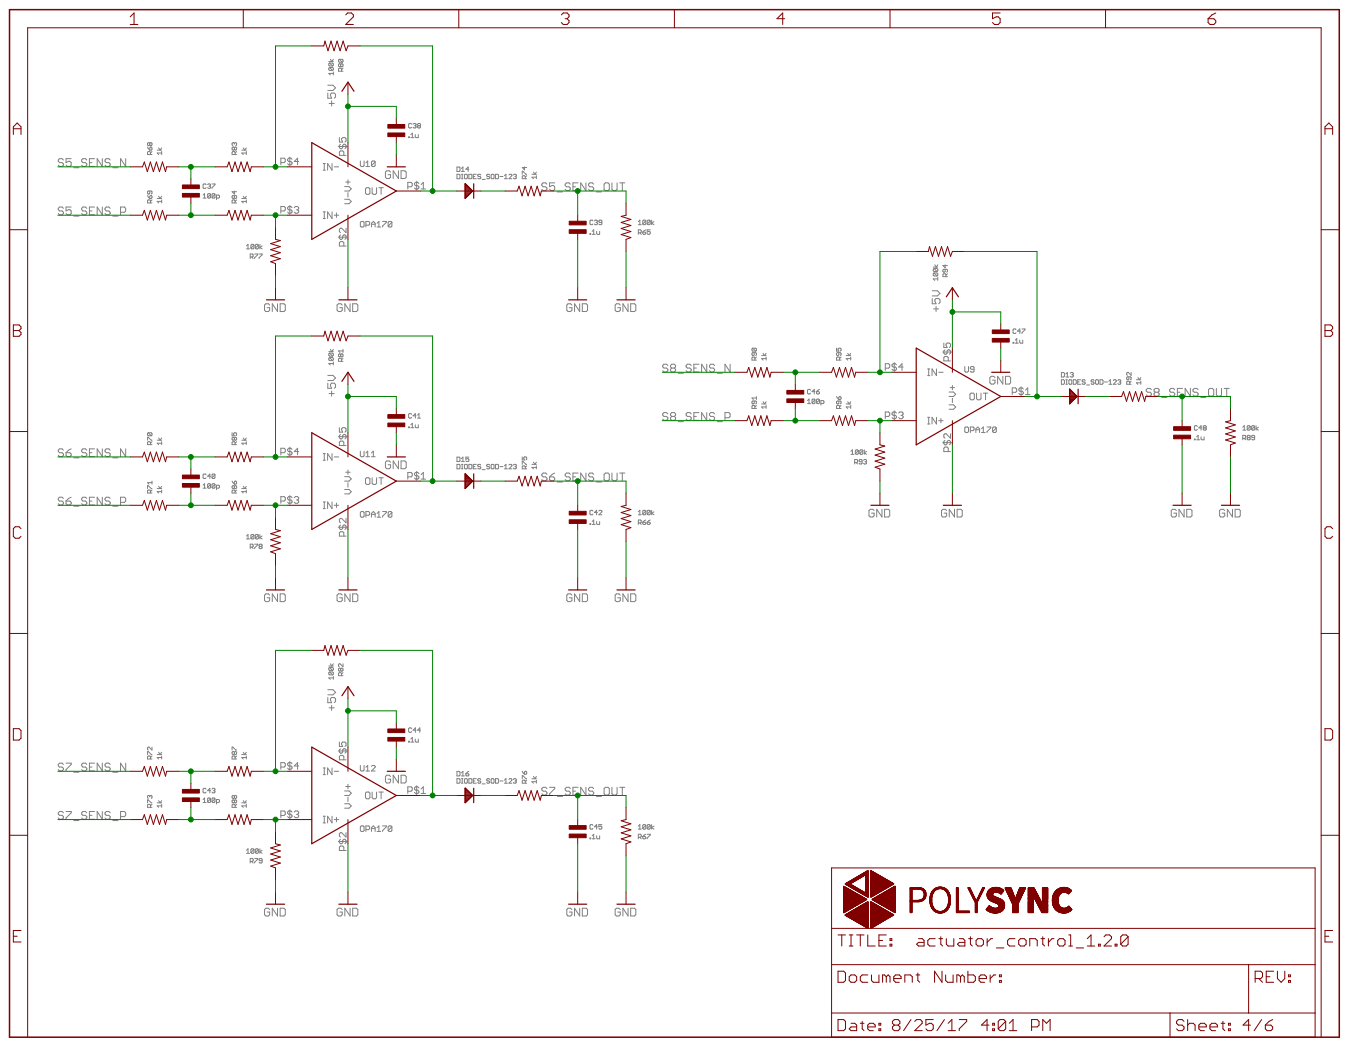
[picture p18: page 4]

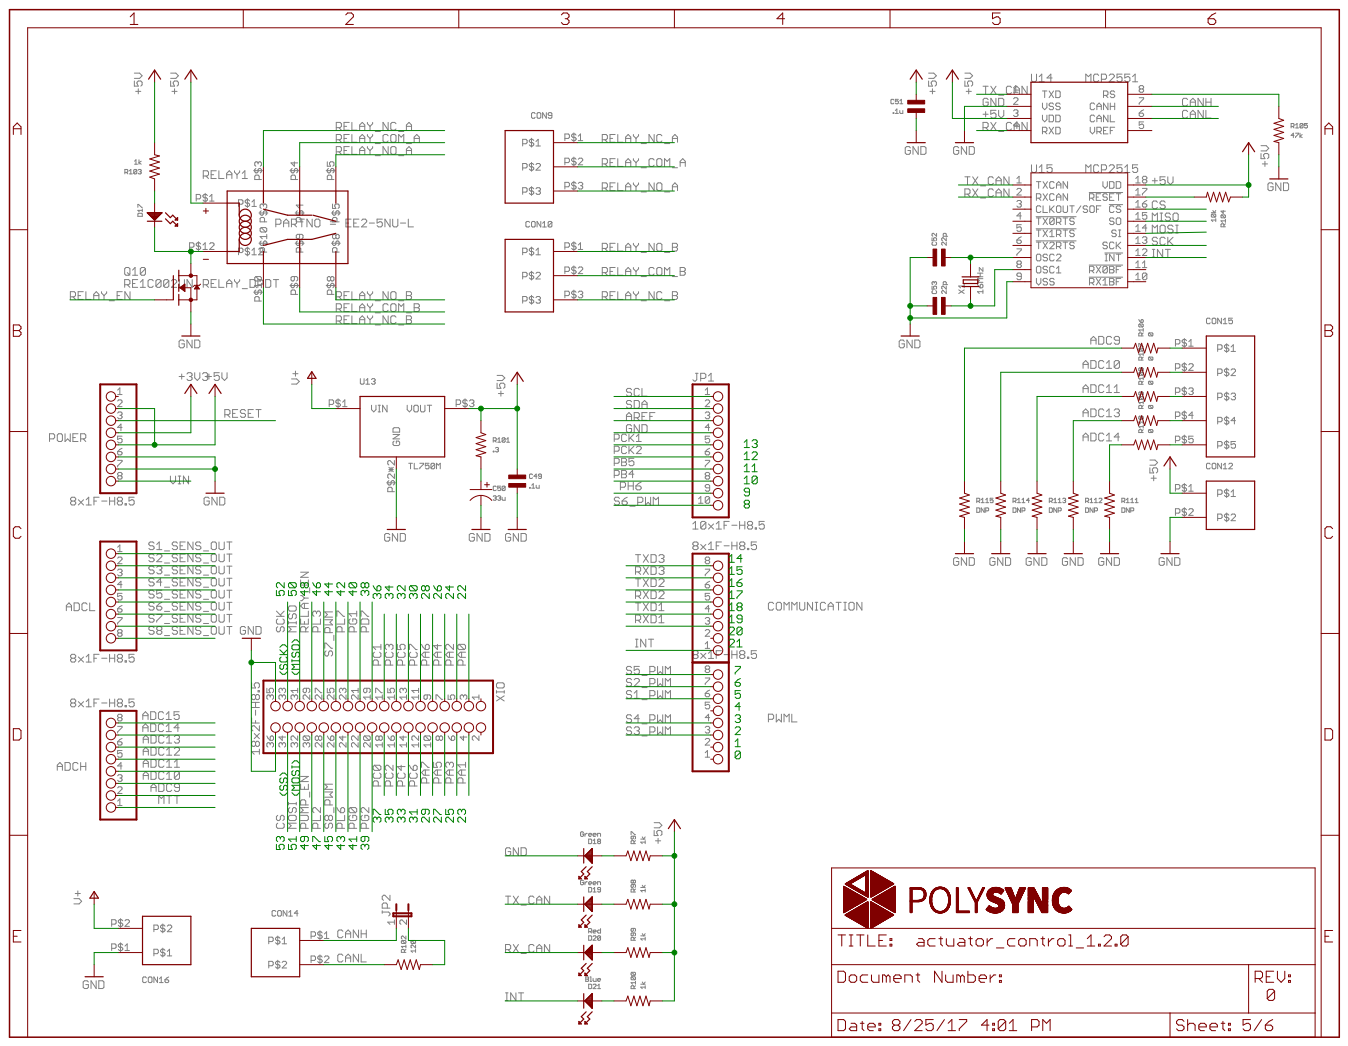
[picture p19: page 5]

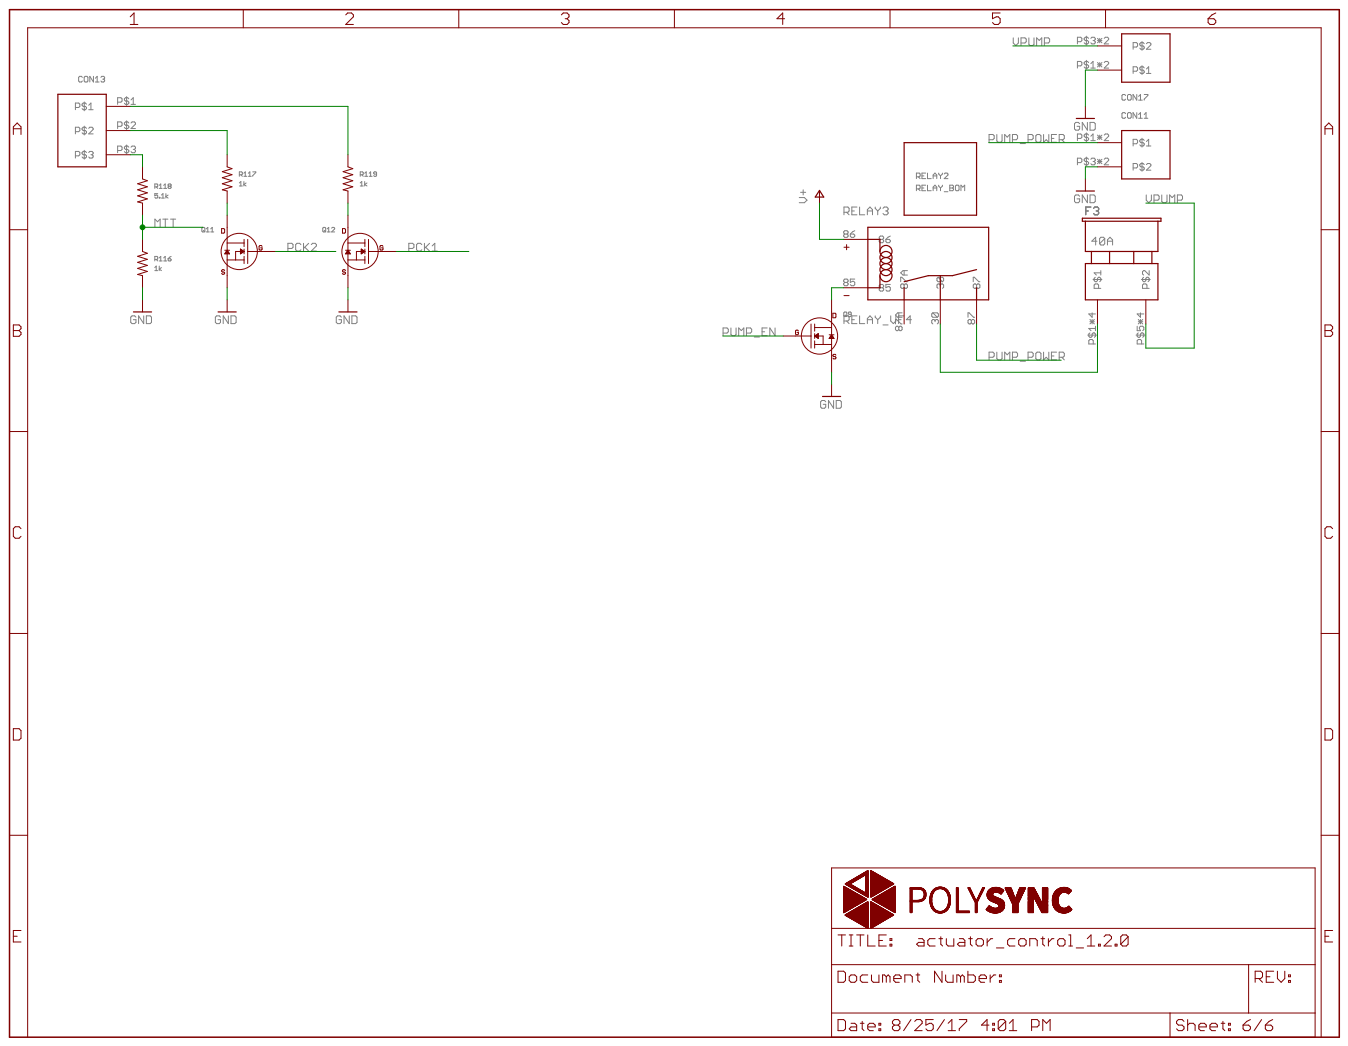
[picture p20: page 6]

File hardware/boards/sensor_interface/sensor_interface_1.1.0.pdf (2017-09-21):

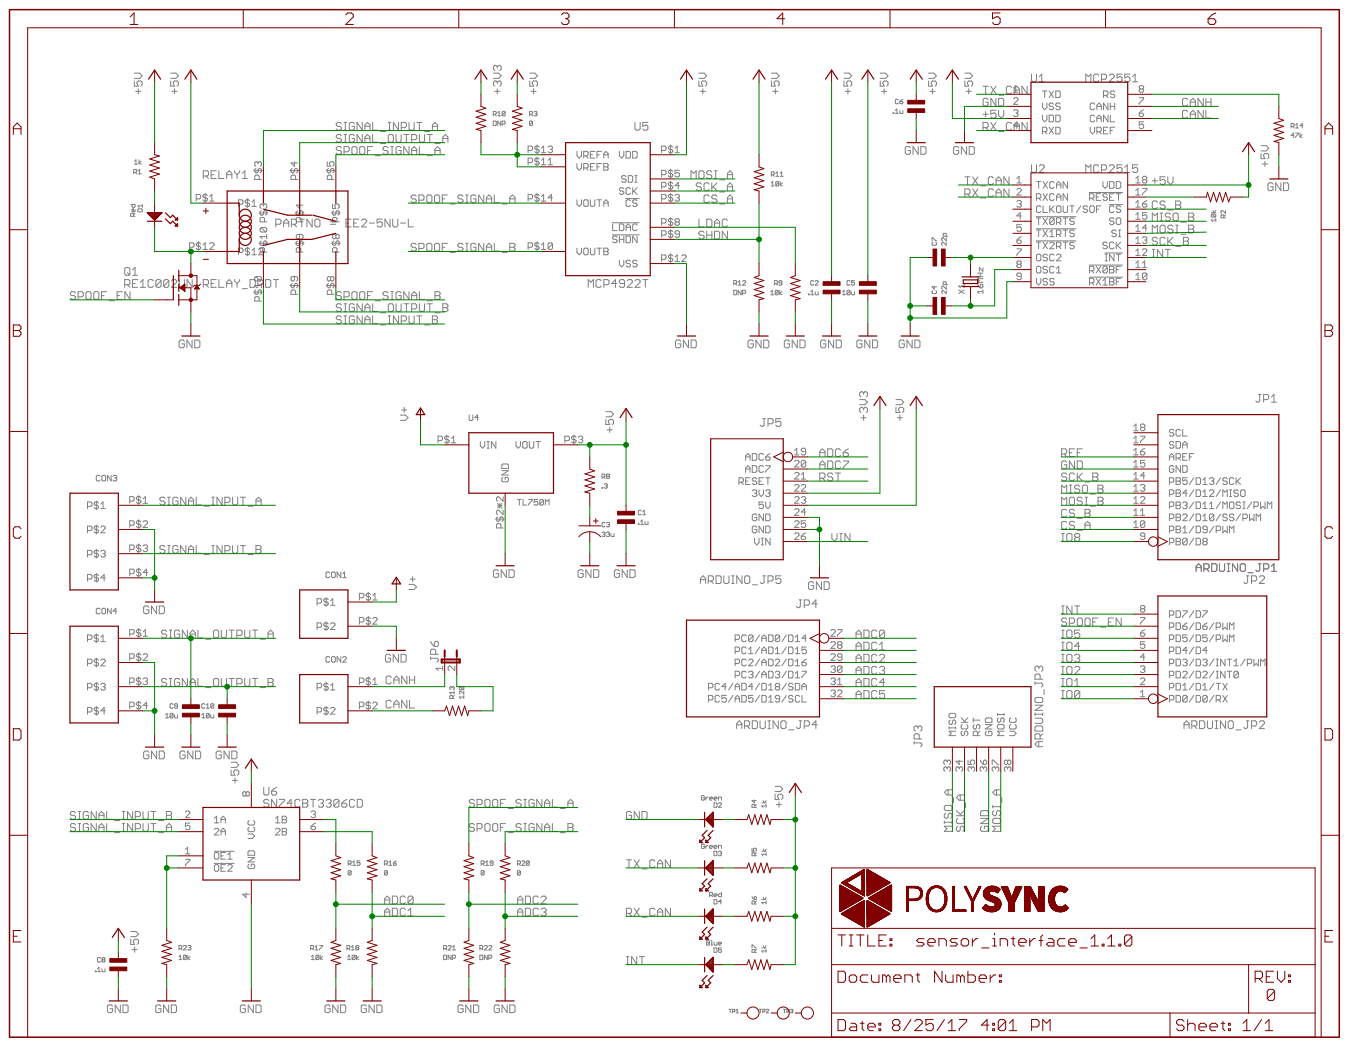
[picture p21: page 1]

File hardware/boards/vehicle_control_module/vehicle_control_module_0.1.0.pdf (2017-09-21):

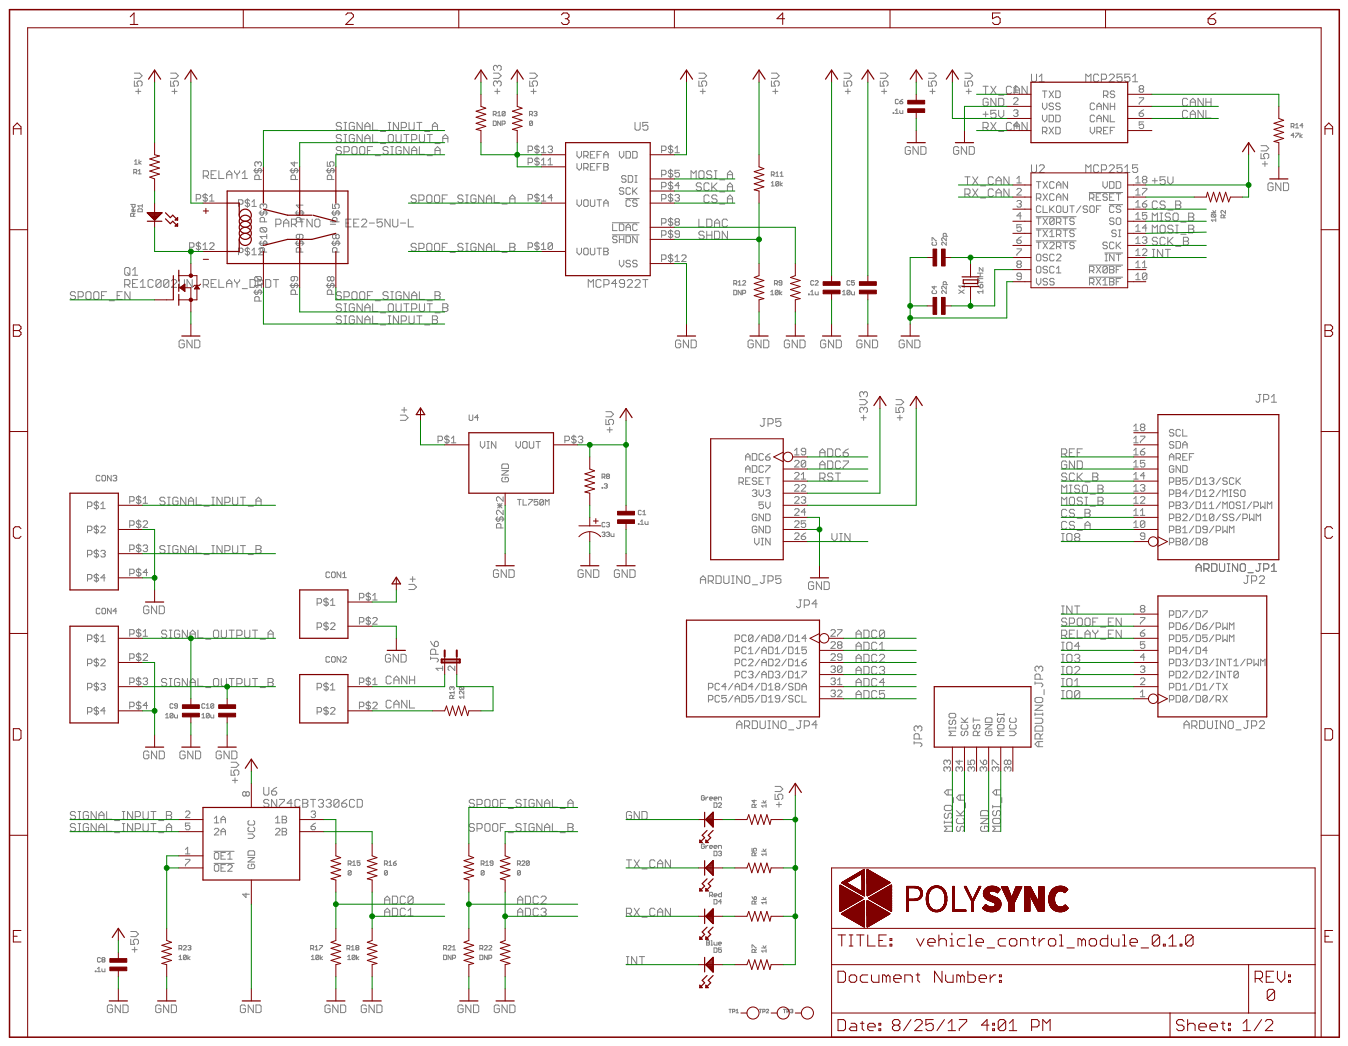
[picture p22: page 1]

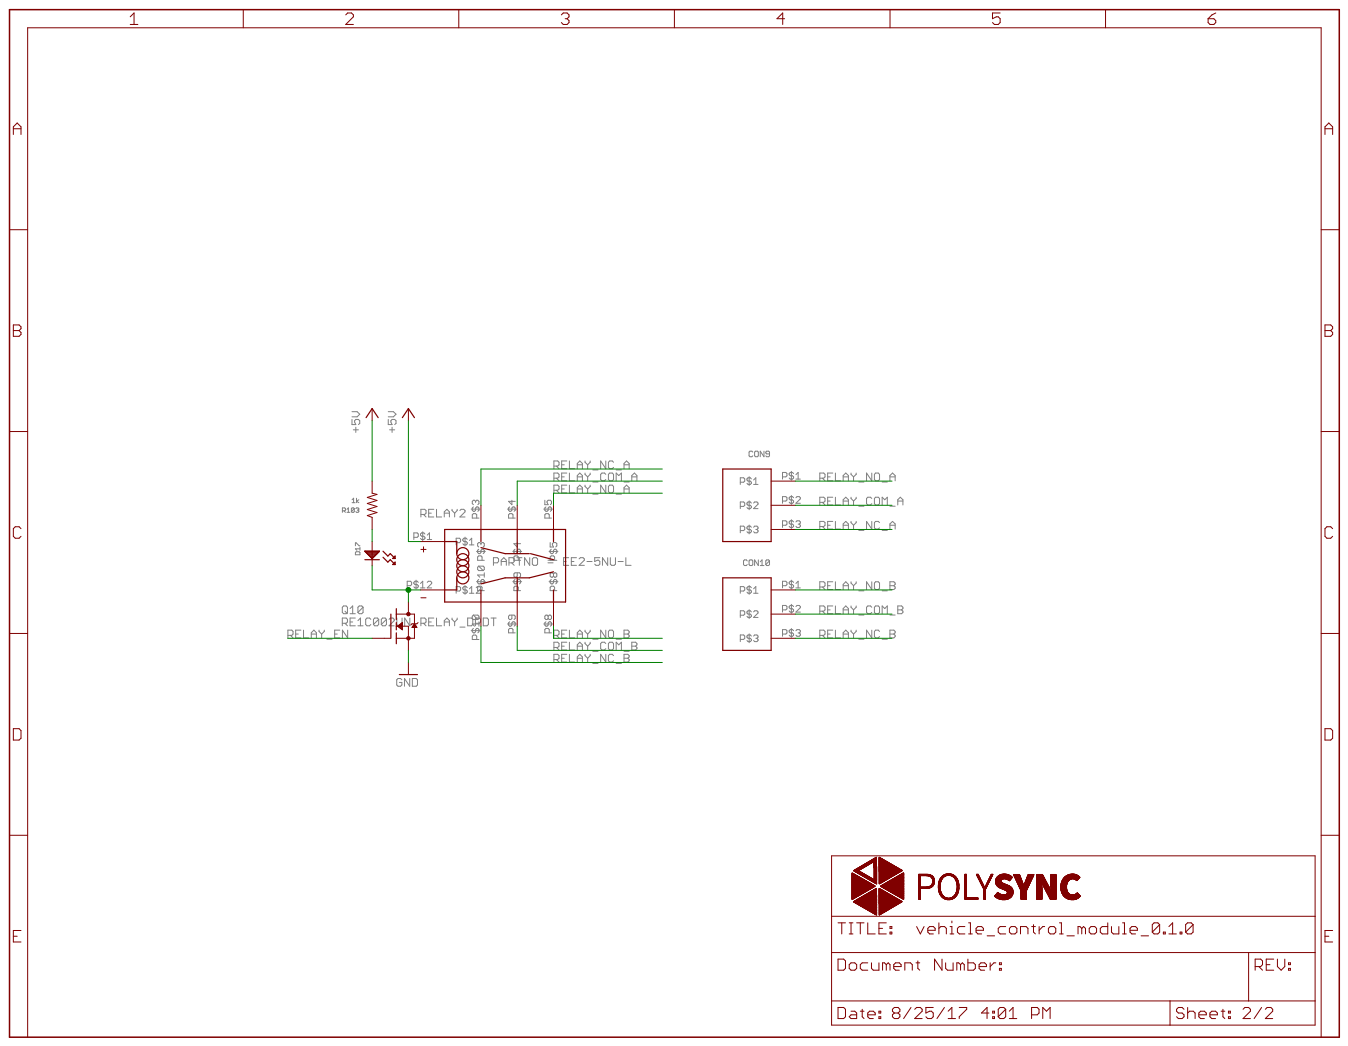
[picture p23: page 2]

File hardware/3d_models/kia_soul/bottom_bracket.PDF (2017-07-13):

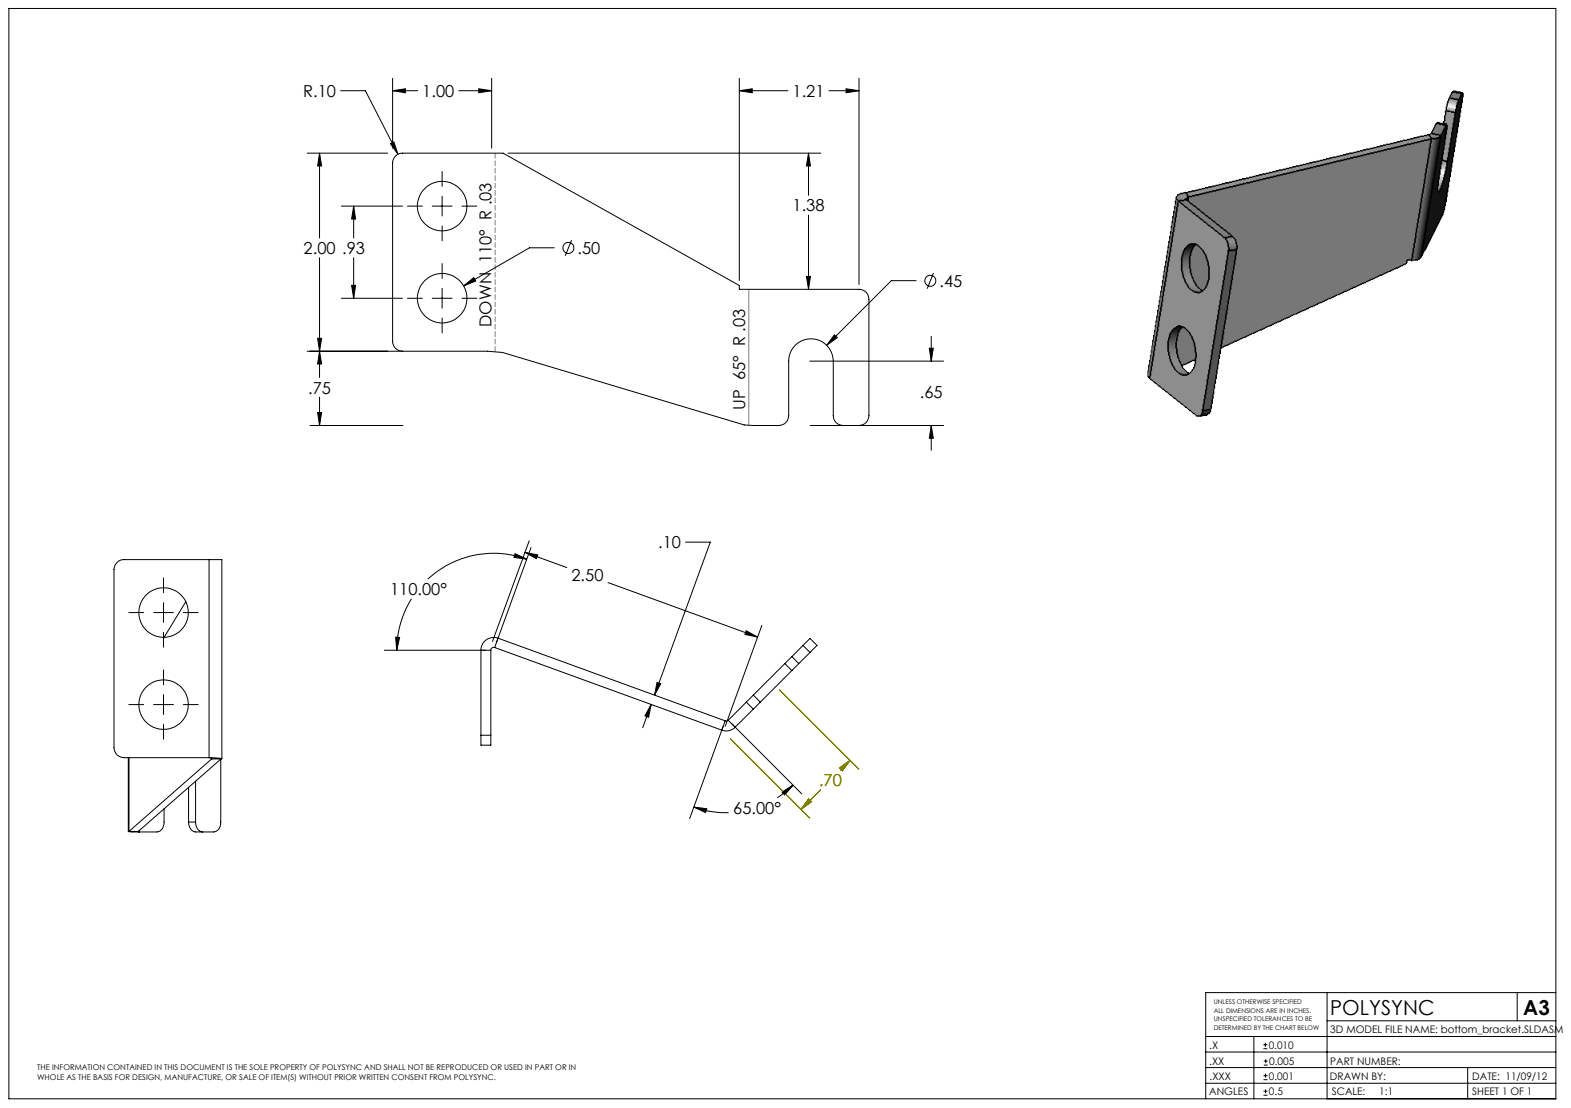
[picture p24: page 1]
DOWN 110° R .03

UNLESS OTHERWISE SPECIFIED
ALL DIMENSIONS ARE IN INCHES.
UNSPECIFIED TOLERANCES TO BE
DETERMINED BY THE CHART BELOW

3D MODEL FILE NAME: bottom_bracket.SLDASM

.X | 0.010
.XX | 0.005 | PART NUMBER:
.XXX | 0.001 | DRAWN BY: | DATE: 11/09/12
ANGLES | 0.5 | SCALE: 1:1 | SHEET 1 OF 1

THE INFORMATION CONTAINED IN THIS DOCUMENT IS THE SOLE PROPERTY OF POLYSYNC AND SHALL NOT BE REPRODUCED OR USED IN PART OR IN
WHOLE AS THE BASIS FOR DESIGN, MANUFACTURE, OR SALE OF ITEM(S) WITHOUT PRIOR WRITTEN CONSENT FROM POLYSYNC.

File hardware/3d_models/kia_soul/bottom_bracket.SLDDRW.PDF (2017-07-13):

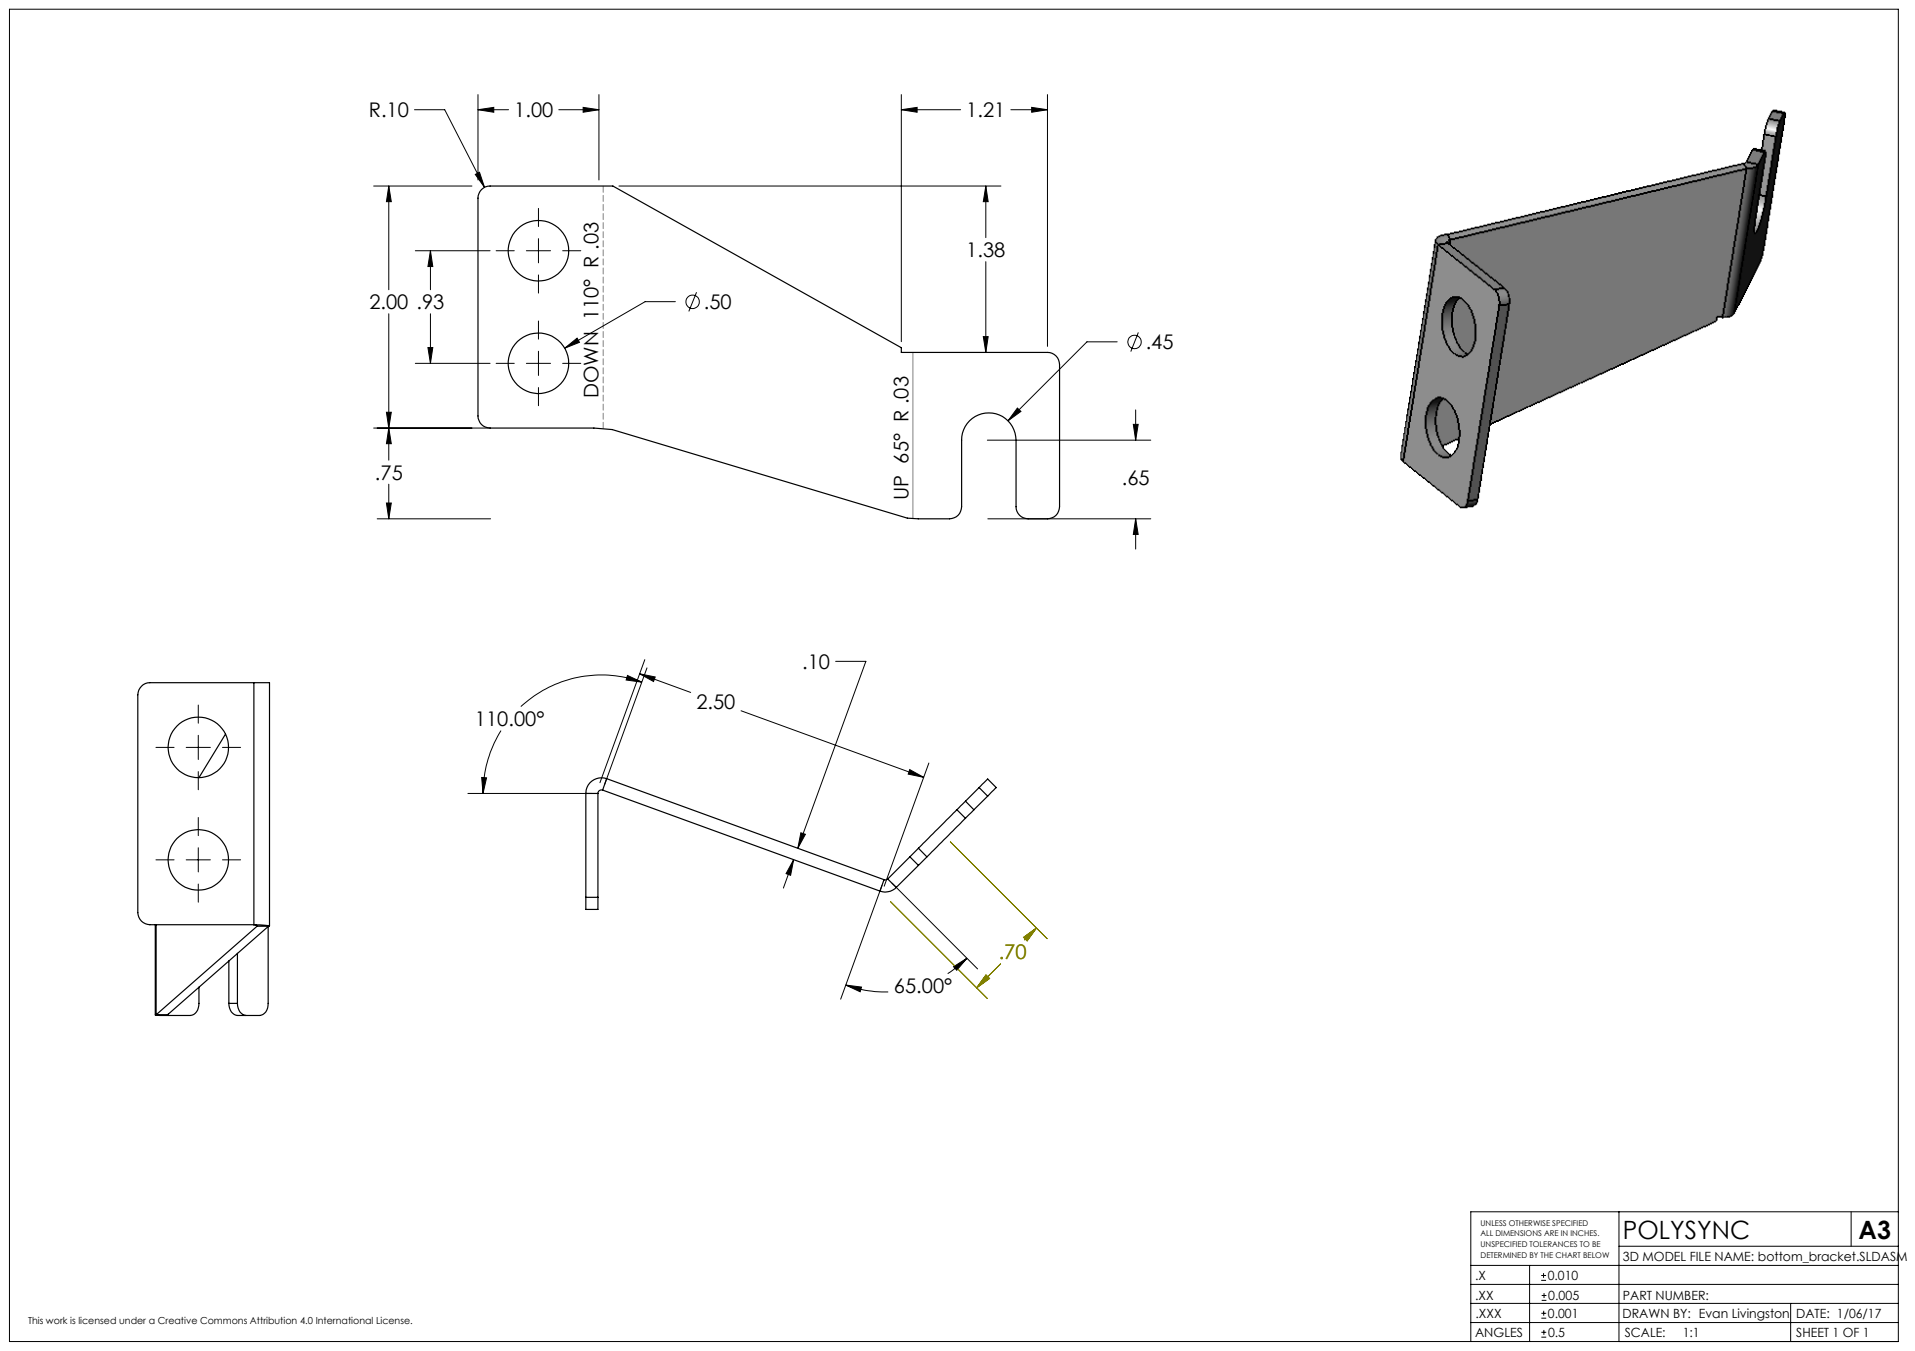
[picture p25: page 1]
DOWN 110° R .03

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

3D MODEL FILE NAME: bottom_bracket.SLDASM

.X | 0.010
.XX | 0.005 | PART NUMBER:
.XXX | 0.001 | DRAWN BY: Evan Livingston | DATE: 1/06/17
ANGLES | 0.5 | SCALE: 1:1 | SHEET 1 OF 1

This work is licensed under a Creative Commons Attribution 4.0 International License.

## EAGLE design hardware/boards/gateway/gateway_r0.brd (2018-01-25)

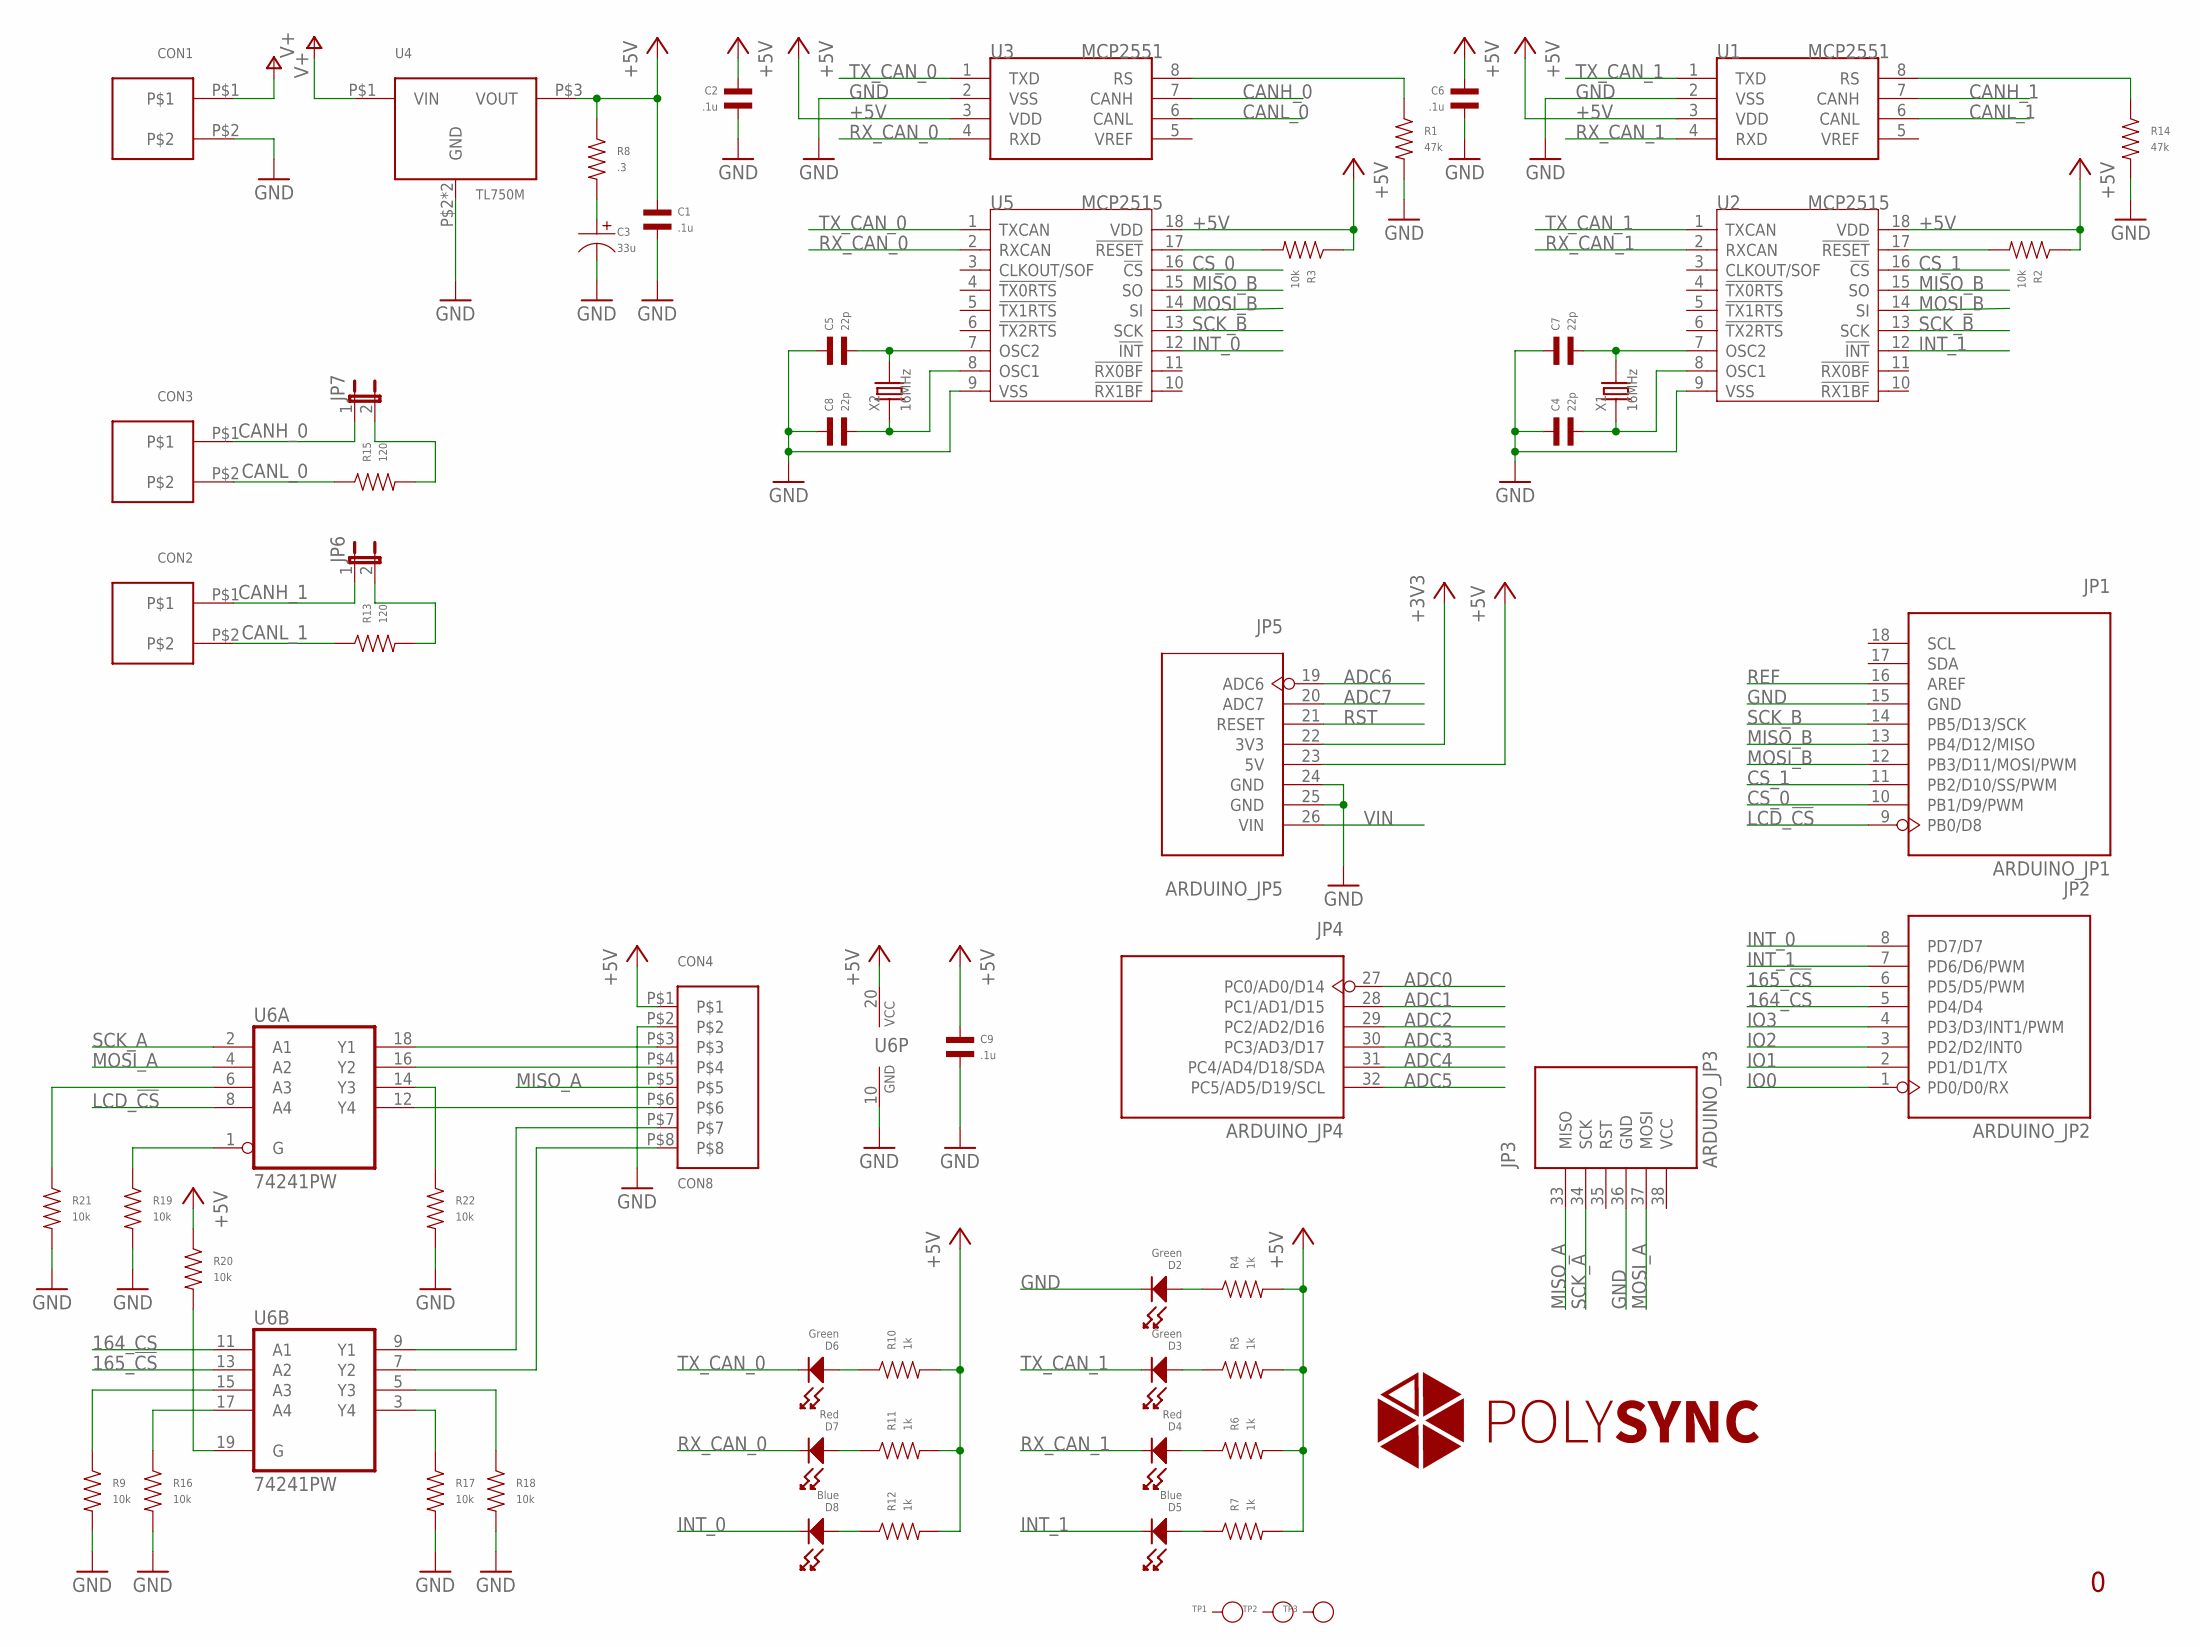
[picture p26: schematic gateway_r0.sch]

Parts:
C1, C2, C6, C9: .1u; C0402
C3: 33u; CP1206
C4, C5, C7, C8: 22p; C0402
CON1, CON2, CON3: CON23.5MM; PHOENIX_2_45
CON4: CON8; PH-8-SM
D2, D3, D6: Green; LED0603
D4, D7: Red; LED0603
D5, D8: Blue; LED0603
JP1: ARDUINO_JP1
JP2: ARDUINO_JP2
JP3: ARDUINO_JP3
JP4: ARDUINO_JP4
JP5: ARDUINO_JP5
JP6, JP7: JP1E; JP1
R1, R14: 47k; R0402
R2, R3, R9, R16, R17, R18, R19, R20, R21, R22: 10k; R0402
R4, R5, R6, R7, R10, R11, R12: 1k; R0402
R8: .3; R0402
R13, R15: 120; R0402
TP1, TP2, TP3: PAD-TEST-POINT'4545'; TP_4545
U1, U3: MCP2551; SOIC8-6.0
U2, U5: MCP2515; SOIC18
U4: TL750M; TO-263
U6: 74241PW; PW_R-PDSO-G20
X1, X2: 16MHz; HC49UP

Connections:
164_CS: JP2.5 (PD4/D4), U6.11 (A1)
165_!CS: JP2.6 (PD5/D5/PWM), U6.13 (A2)
+3V3: JP5.22 (3V3)
+5V: C1.P$1, C2.P$1, C6.P$1, C9.P$1, CON4.P$1, JP5.23 (5V), R2.P$1, R3.P$1, R4.P$2, R5.P$2, R6.P$2, R7.P$2, R8.P$1, R10.P$2, R11.P$2, R12.P$2, R20.P$1, U1.3 (VDD), U2.18 (VDD), U3.3 (VDD), U4.P$3 (VOUT), U5.18 (VDD), U6.20 (VCC)
ADC0: JP4.27 (PC0/AD0/D14)
ADC1: JP4.28 (PC1/AD1/D15)
ADC2: JP4.29 (PC2/AD2/D16)
ADC3: JP4.30 (PC3/AD3/D17)
ADC4: JP4.31 (PC4/AD4/D18/SDA)
ADC5: JP4.32 (PC5/AD5/D19/SCL)
ADC6: JP5.19 (ADC6)
ADC7: JP5.20 (ADC7)
CANH_0: CON3.P$1, JP7.1, U3.7 (CANH)
CANH_1: CON2.P$1, JP6.1, U1.7 (CANH)
CANL_0: CON3.P$2, R15.P$1, U3.6 (CANL)
CANL_1: CON2.P$2, R13.P$1, U1.6 (CANL)
CS_0: JP1.10 (PB1/D9/PWM), U5.16 (!CS)
CS_1: JP1.11 (PB2/D10/SS/PWM), U2.16 (!CS)
GND: C1.P$2, C2.P$2, C3.P$2, C4.P$1, C5.P$1, C6.P$2, C7.P$1, C8.P$1, C9.P$2, CON1.P$2, CON4.P$2, D2.CATHODE, JP1.15 (GND), JP3.36 (GND), JP5.24 (GND), JP5.25 (GND), R1.P$2, R9.P$2, R14.P$2, R16.P$2, R17.P$2, R18.P$2, R19.P$2, R21.P$2, R22.P$2, U1.2 (VSS), U2.9 (VSS), U3.2 (VSS), U4.P$2 (GND), U4.P$4 (GND), U5.9 (VSS), U6.10 (GND)
INT_0: D8.CATHODE, JP2.8 (PD7/D7), U5.12 (!INT)
INT_1: D5.CATHODE, JP2.7 (PD6/D6/PWM), U2.12 (!INT)
IO0: JP2.1 (PD0/D0/RX)
IO1: JP2.2 (PD1/D1/TX)
IO2: JP2.3 (PD2/D2/INT0)
IO3: JP2.4 (PD3/D3/INT1/PWM)
LCD_!CS: JP1.9 (PB0/D8), U6.8 (A4)
MISO_A: CON4.P$5, JP3.33 (MISO)
MISO_B: JP1.13 (PB4/D12/MISO), U2.15 (SO), U5.15 (SO)
MOSI_A: JP3.37 (MOSI), U6.4 (A2)
MOSI_B: JP1.12 (PB3/D11/MOSI/PWM), U2.14 (SI), U5.14 (SI)
unnamed: D3.ANODE, R5.P$1
unnamed: JP6.2, R13.P$2
unnamed: C5.P$2, U5.7 (OSC2), X2.2
unnamed: C3.P$1, R8.P$2
unnamed: D4.ANODE, R6.P$1
unnamed: D2.ANODE, R4.P$1
unnamed: C8.P$2, U5.8 (OSC1), X2.1
unnamed: D5.ANODE, R7.P$1
unnamed: R14.P$1, U1.8 (RS)
unnamed: R1.P$1, U3.8 (RS)
unnamed: CON4.P$3, U6.18 (Y1)
unnamed: D6.ANODE, R10.P$1
unnamed: D7.ANODE, R11.P$1
unnamed: D8.ANODE, R12.P$1
unnamed: JP7.2, R15.P$2
unnamed: C7.P$2, U2.7 (OSC2), X1.2
unnamed: C4.P$2, U2.8 (OSC1), X1.1
unnamed: CON4.P$4, U6.16 (Y2)
unnamed: R21.P$1, U6.6 (A3)
unnamed: CON4.P$6, U6.12 (Y4)
unnamed: CON4.P$7, U6.9 (Y1)
unnamed: CON4.P$8, U6.7 (Y2)
unnamed: R9.P$1, U6.15 (A3)
unnamed: R16.P$1, U6.17 (A4)
unnamed: R17.P$1, U6.3 (Y4)
unnamed: R18.P$1, U6.5 (Y3)
unnamed: R19.P$1, U6.1 (G)
unnamed: R20.P$2, U6.19 (G)
unnamed: R22.P$1, U6.14 (Y3)
REF: JP1.16 (AREF)
RST: JP5.21 (RESET)
RST_N: R2.P$2, U2.17 (!RESET)
RST_N1: R3.P$2, U5.17 (!RESET)
RX_CAN_0: D7.CATHODE, U3.4 (RXD), U5.2 (RXCAN)
RX_CAN_1: D4.CATHODE, U1.4 (RXD), U2.2 (RXCAN)
SCK_A: JP3.34 (SCK), U6.2 (A1)
SCK_B: JP1.14 (PB5/D13/SCK), U2.13 (SCK), U5.13 (SCK)
TX_CAN_0: D6.CATHODE, U3.1 (TXD), U5.1 (TXCAN)
TX_CAN_1: D3.CATHODE, U1.1 (TXD), U2.1 (TXCAN)
V+: CON1.P$1, U4.P$1 (VIN)
VIN: JP5.26 (VIN)

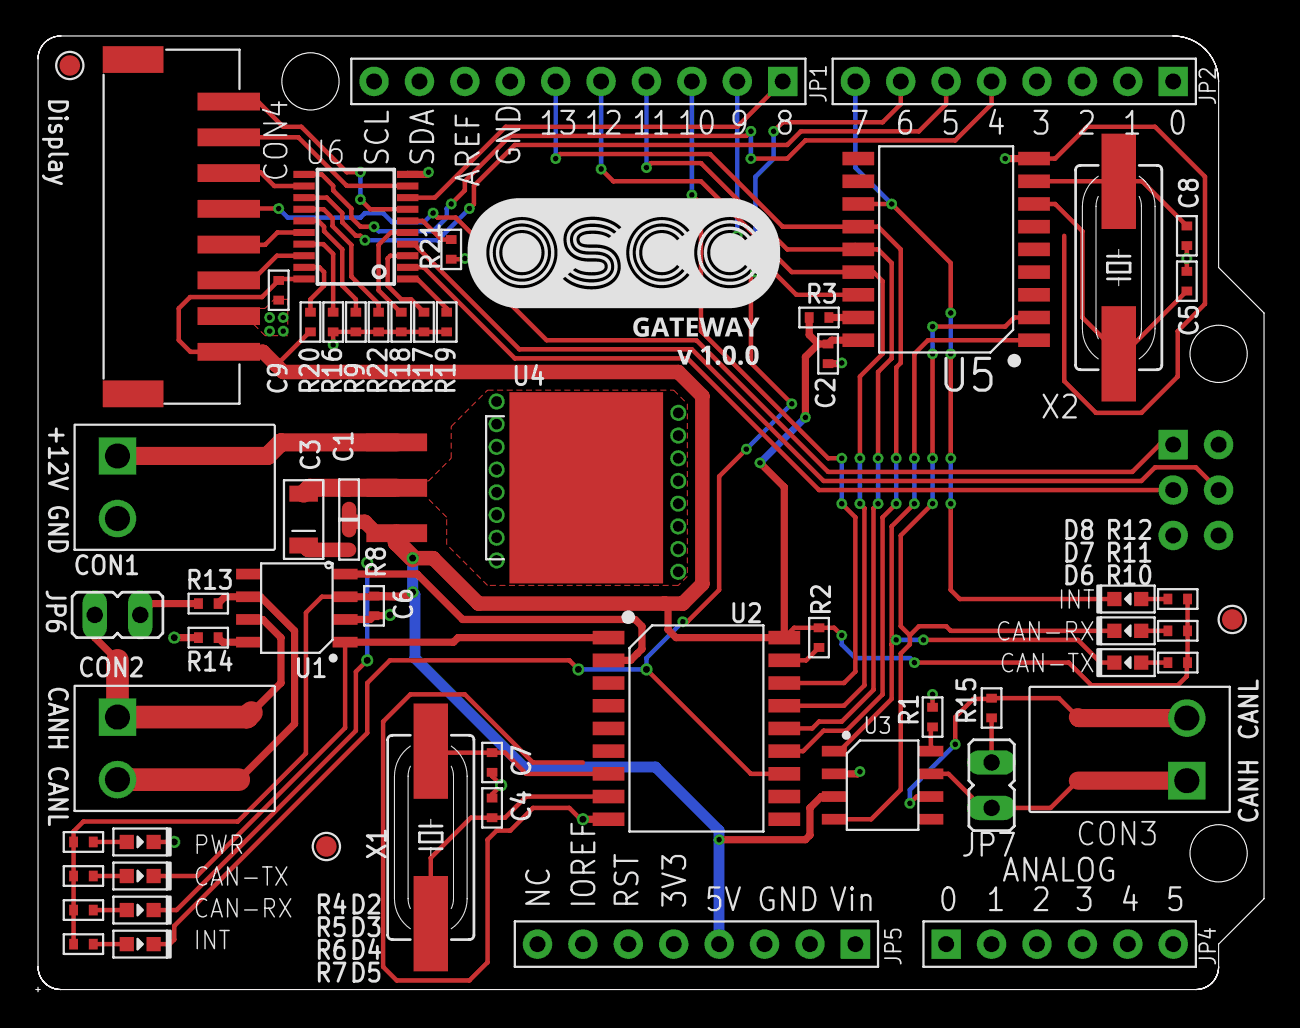
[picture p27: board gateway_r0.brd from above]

Board: 2 copper layers, 68.6 x 53.3 mm, 62 parts (0 on the bottom side), 55 nets.

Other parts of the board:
U$1: POLYSYNC_STEERING_BOT
U$2: POLYSYNC_GATEWAY_1_0_0

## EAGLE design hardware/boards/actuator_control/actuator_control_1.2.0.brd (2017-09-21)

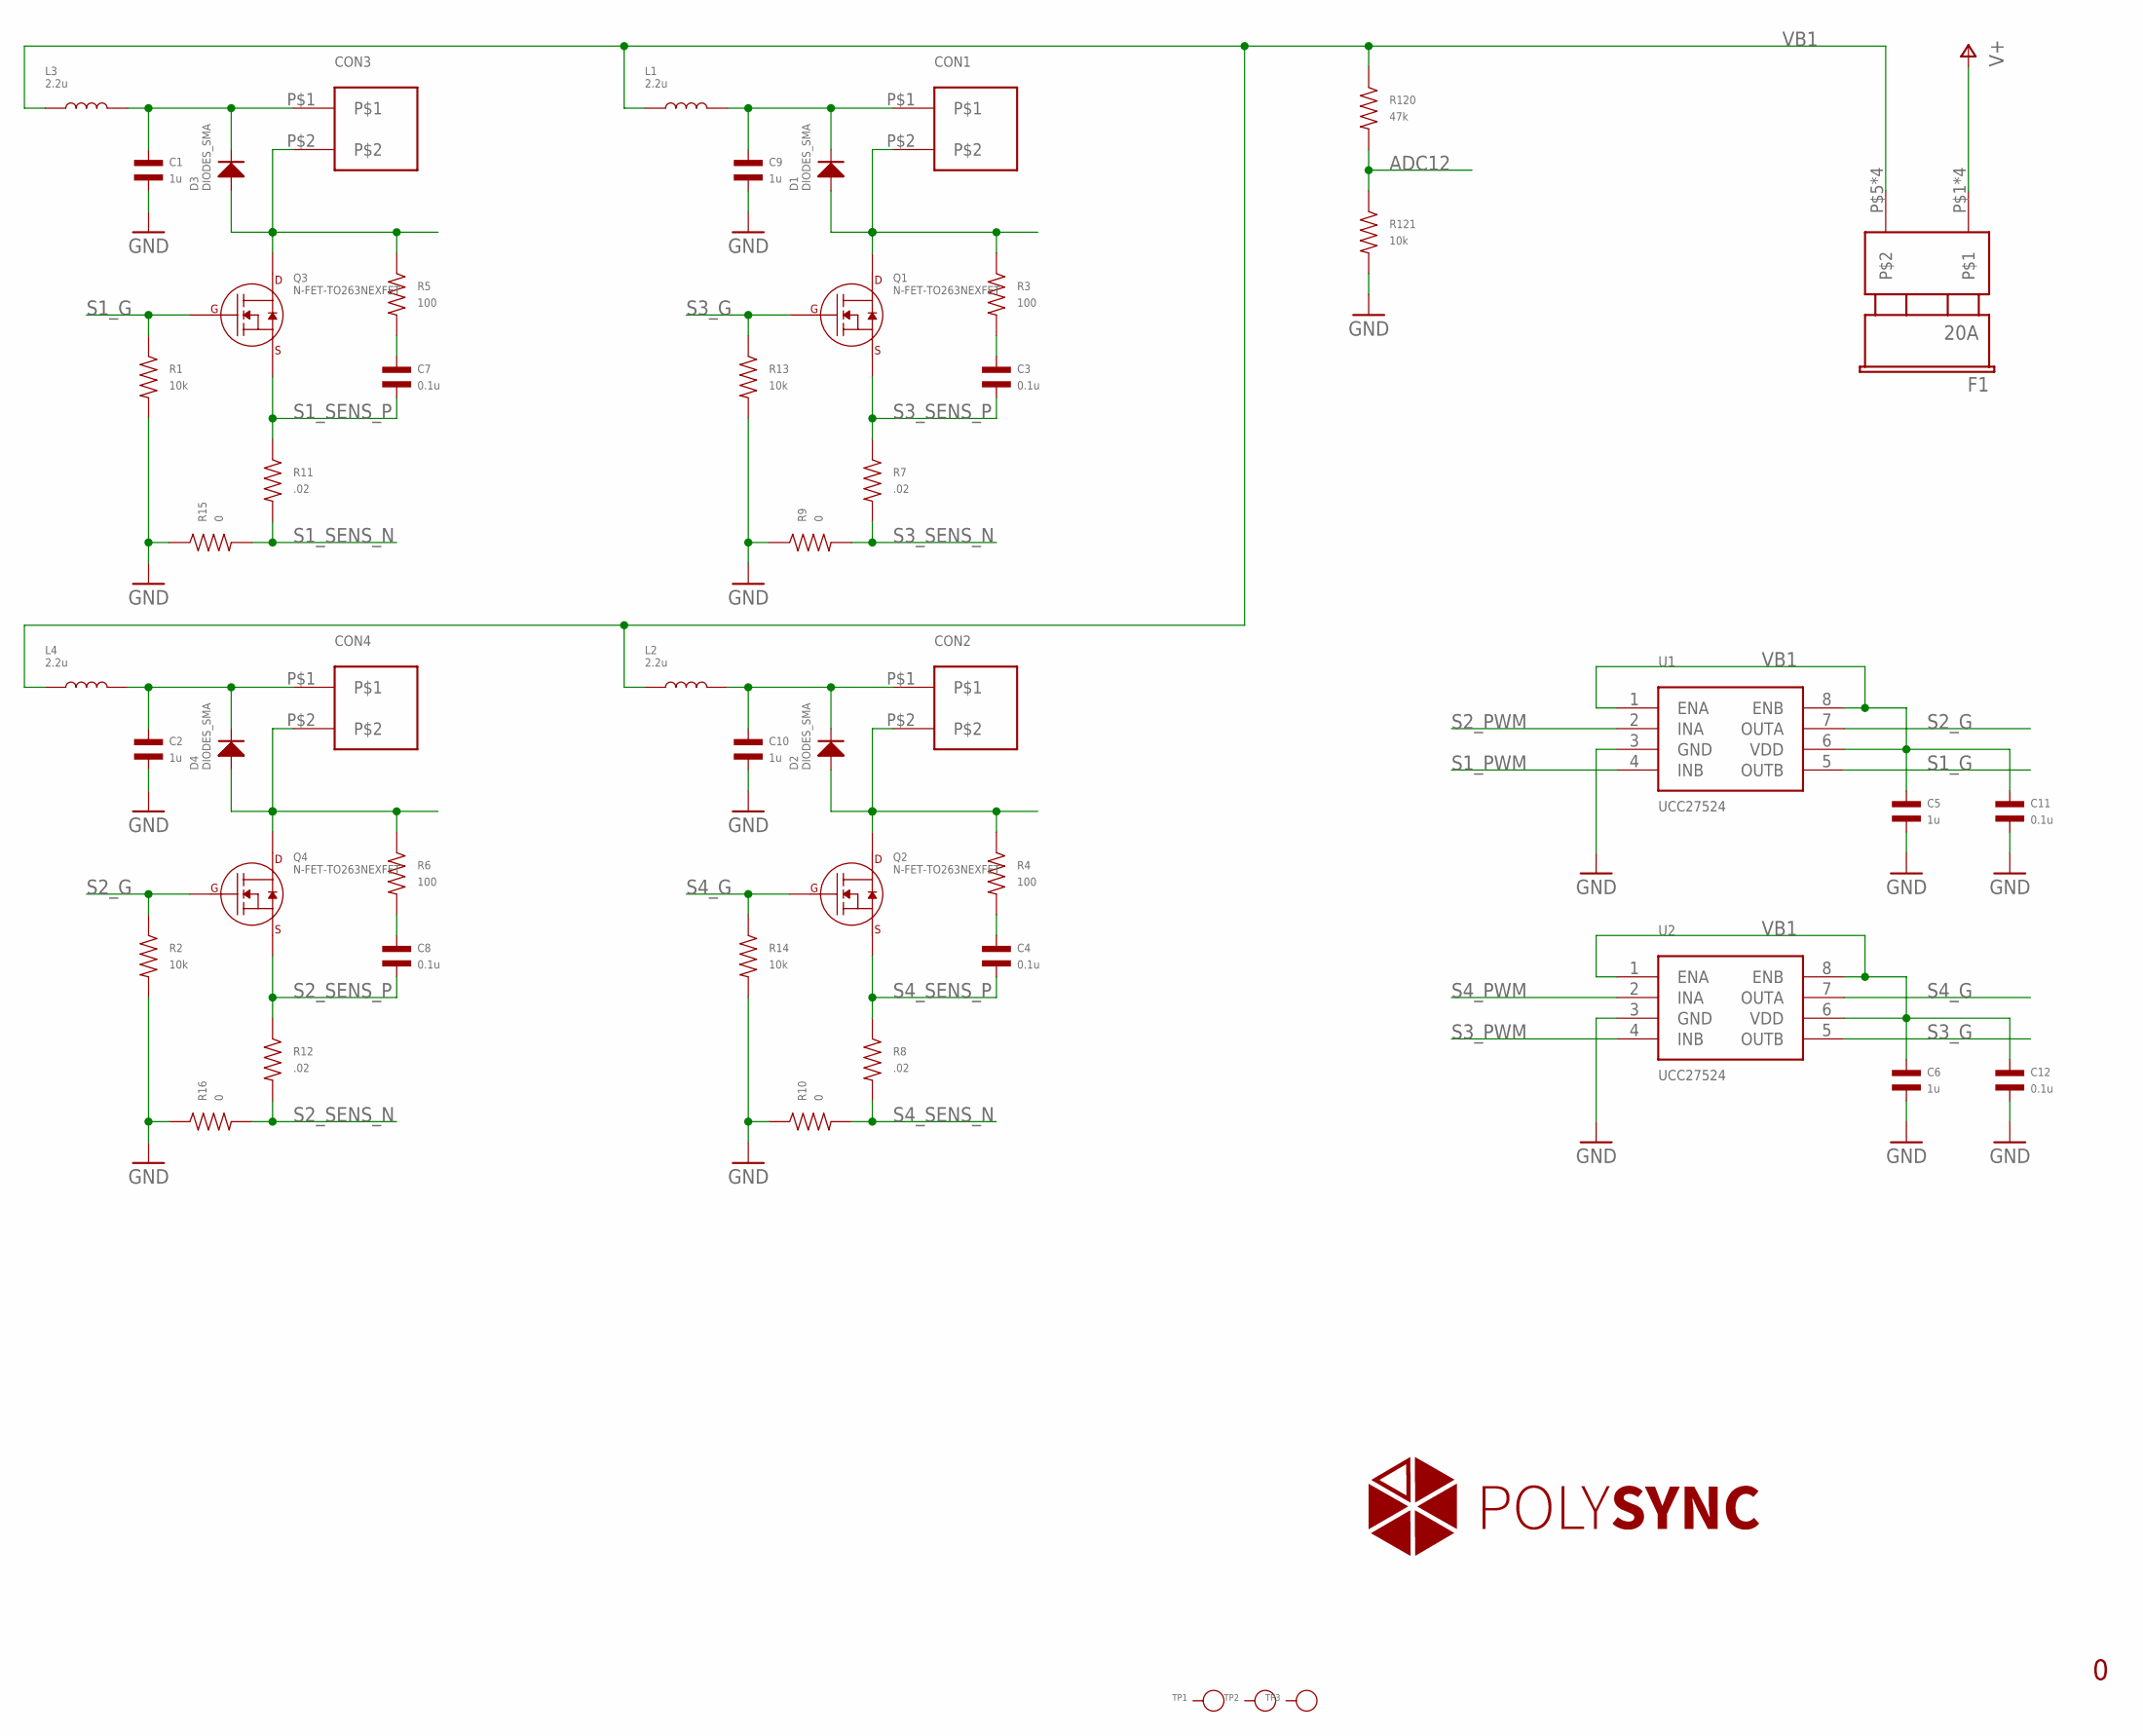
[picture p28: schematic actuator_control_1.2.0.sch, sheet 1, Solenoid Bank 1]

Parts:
C1, C2, C5, C6, C9, C10: 1u; C1206
C3, C4, C7, C8, C11, C12: 0.1u; C0805
CON1, CON2, CON3, CON4: CON23.5MM; PHOENIX_2_45
D1, D2, D4: DIODES_SMA; SMA
D3: DIODES_SMA; SMA; MPN US1B-13-F
F1: 20A; FUSE_ATO; PARTNO 178.6165.0001
L1, L2, L3, L4: 2.2u; SRP7050; PARTNO SRP7050TA-2R2M
Q1, Q2, Q3, Q4: N-FET-TO263NEXFET; SON8-DQJ
R1, R2, R13, R14, R121: 10k; R0402
R3, R4, R5, R6: 100; R0805
R7, R8, R11, R12: .02; R1206
R9, R10, R15, R16: 0; R0805
R120: 47k; R0402
TP1, TP2, TP3: PAD-TEST-POINT'4545'; TP_4545
U1, U2: UCC27524; SOIC-8

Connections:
ADC12: R120.P$2, R121.P$1; also elsewhere on the board
GND: C1.P$2, C2.P$2, C5.P$2, C6.P$2, C9.P$2, C10.P$2, C11.P$2, C12.P$2, R1.P$2, R2.P$2, R9.P$1, R10.P$1, R13.P$2, R14.P$2, R15.P$1, R16.P$1, R121.P$2, U1.3 (GND), U2.3 (GND); also elsewhere on the board
unnamed: C1.P$1, CON3.P$1, D3.CATHODE, L3.P$2
unnamed: CON3.P$2, D3.ANODE, Q3.P$5 (DRAIN), Q3.P$6 (DRAIN), Q3.P$7 (DRAIN), Q3.P$8 (DRAIN), Q3.P$9 (DRAIN), R5.P$1
unnamed: C7.P$1, R5.P$2
unnamed: C2.P$1, CON4.P$1, D4.CATHODE, L4.P$2
unnamed: CON4.P$2, D4.ANODE, Q4.P$5 (DRAIN), Q4.P$6 (DRAIN), Q4.P$7 (DRAIN), Q4.P$8 (DRAIN), Q4.P$9 (DRAIN), R6.P$1
unnamed: C8.P$1, R6.P$2
unnamed: C9.P$1, CON1.P$1, D1.CATHODE, L1.P$2
unnamed: CON1.P$2, D1.ANODE, Q1.P$5 (DRAIN), Q1.P$6 (DRAIN), Q1.P$7 (DRAIN), Q1.P$8 (DRAIN), Q1.P$9 (DRAIN), R3.P$1
unnamed: C3.P$1, R3.P$2
unnamed: C10.P$1, CON2.P$1, D2.CATHODE, L2.P$2
unnamed: CON2.P$2, D2.ANODE, Q2.P$5 (DRAIN), Q2.P$6 (DRAIN), Q2.P$7 (DRAIN), Q2.P$8 (DRAIN), Q2.P$9 (DRAIN), R4.P$1
unnamed: C4.P$1, R4.P$2
S1_G: Q3.P$4 (GATE), R1.P$1, U1.5 (OUTB)
S1_PWM: U1.4 (INB); also elsewhere on the board
S1_SENS_N: R11.P$2, R15.P$2; also elsewhere on the board
S1_SENS_P: C7.P$2, Q3.P$1 (SOURCE), Q3.P$2 (SOURCE), Q3.P$3 (SOURCE), R11.P$1; also elsewhere on the board
S2_G: Q4.P$4 (GATE), R2.P$1, U1.7 (OUTA)
S2_PWM: U1.2 (INA); also elsewhere on the board
S2_SENS_N: R12.P$2, R16.P$2; also elsewhere on the board
S2_SENS_P: C8.P$2, Q4.P$1 (SOURCE), Q4.P$2 (SOURCE), Q4.P$3 (SOURCE), R12.P$1; also elsewhere on the board
S3_G: Q1.P$4 (GATE), R13.P$1, U2.5 (OUTB)
S3_PWM: U2.4 (INB); also elsewhere on the board
S3_SENS_N: R7.P$2, R9.P$2; also elsewhere on the board
S3_SENS_P: C3.P$2, Q1.P$1 (SOURCE), Q1.P$2 (SOURCE), Q1.P$3 (SOURCE), R7.P$1; also elsewhere on the board
S4_G: Q2.P$4 (GATE), R14.P$1, U2.7 (OUTA)
S4_PWM: U2.2 (INA); also elsewhere on the board
S4_SENS_N: R8.P$2, R10.P$2; also elsewhere on the board
S4_SENS_P: C4.P$2, Q2.P$1 (SOURCE), Q2.P$2 (SOURCE), Q2.P$3 (SOURCE), R8.P$1; also elsewhere on the board
V+: F1.P$1, F1.P$2, F1.P$3, F1.P$4; also elsewhere on the board
VB1: C5.P$1, C6.P$1, C11.P$1, C12.P$1, F1.P$5, F1.P$6, F1.P$7, F1.P$8, L1.P$1, L2.P$1, L3.P$1, L4.P$1, R120.P$1, U1.1 (ENA), U1.6 (VDD), U1.8 (ENB), U2.1 (ENA), U2.6 (VDD), U2.8 (ENB); also elsewhere on the board

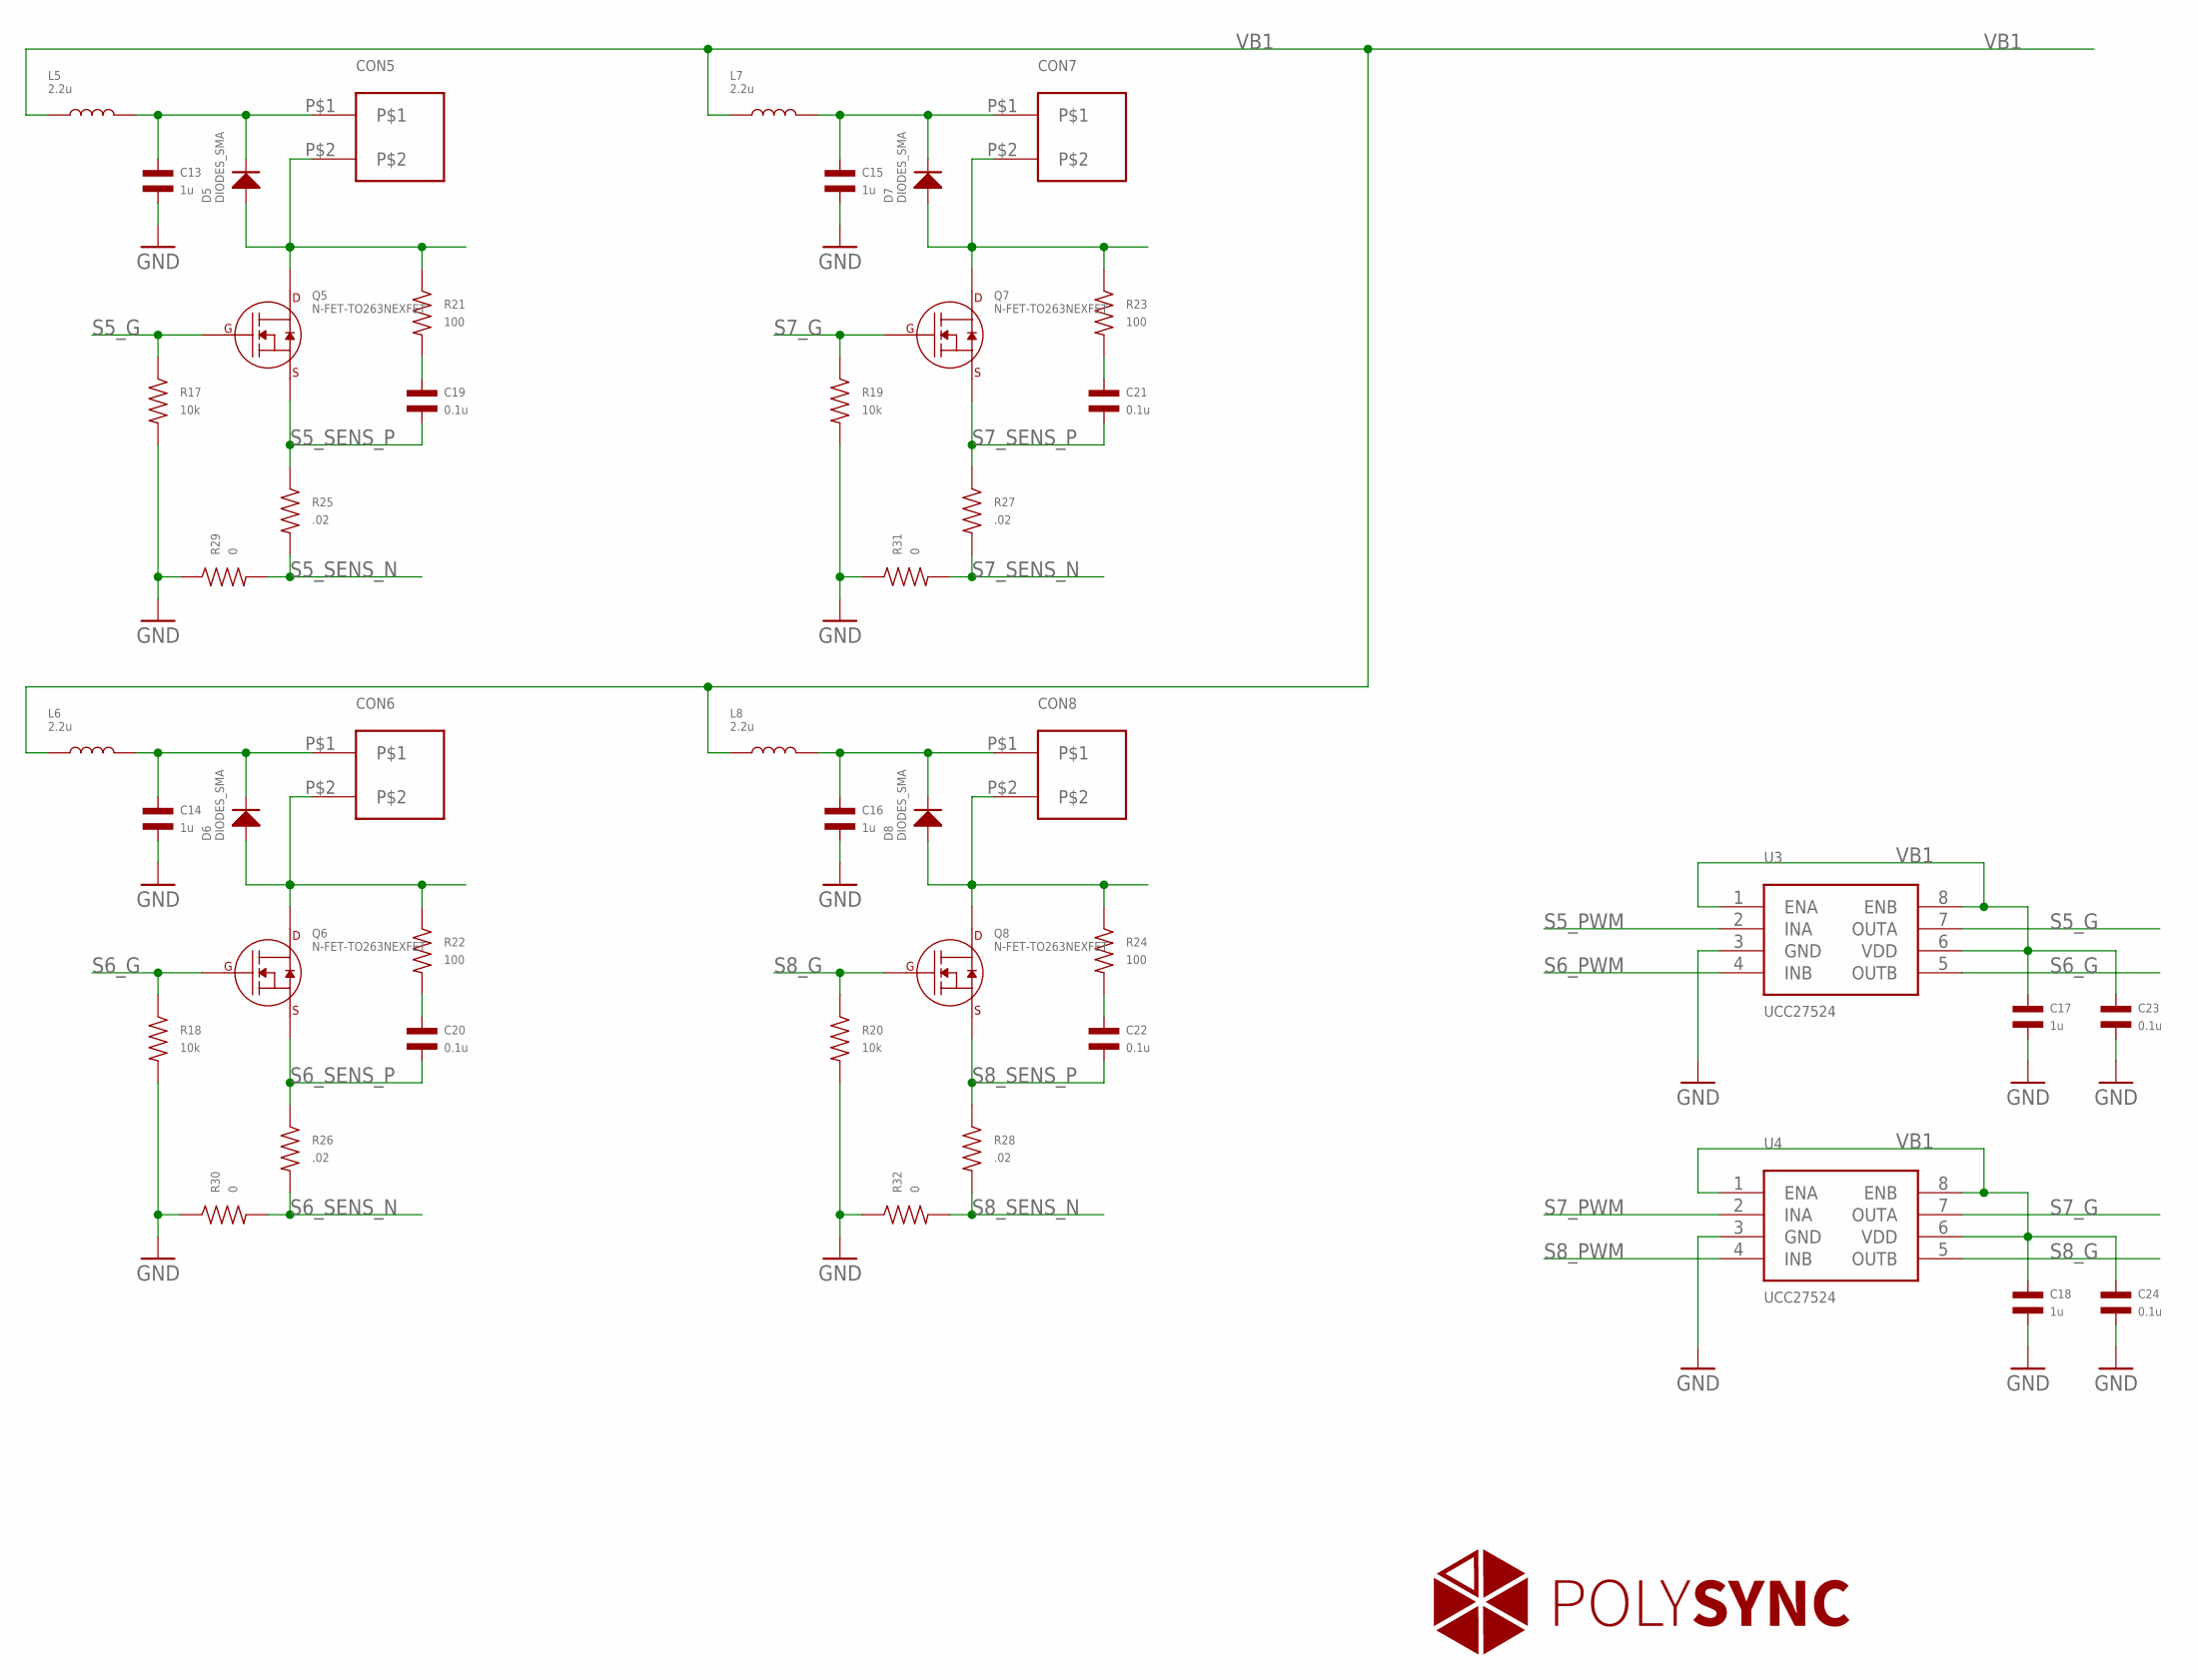
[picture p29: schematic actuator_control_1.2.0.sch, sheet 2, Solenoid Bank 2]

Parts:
C13, C14, C15, C16, C17, C18: 1u; C1206
C19, C20, C21, C22, C23, C24: 0.1u; C0805
CON5, CON6, CON7, CON8: CON23.5MM; PHOENIX_2_45
D5, D6, D7, D8: DIODES_SMA; SMA
L5, L6, L7, L8: 2.2u; SRP7050; PARTNO SRP7050TA-2R2M
Q5, Q6, Q7, Q8: N-FET-TO263NEXFET; SON8-DQJ
R17, R18, R19, R20: 10k; R0402
R21, R22, R23, R24: 100; R0805
R25, R26, R27, R28: .02; R1206
R29, R30, R31, R32: 0; R0805
U3, U4: UCC27524; SOIC-8

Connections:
GND: C13.P$2, C14.P$2, C15.P$2, C16.P$2, C17.P$2, C18.P$2, C23.P$2, C24.P$2, R17.P$2, R18.P$2, R19.P$2, R20.P$2, R29.P$1, R30.P$1, R31.P$1, R32.P$1, U3.3 (GND), U4.3 (GND); also elsewhere on the board
unnamed: C13.P$1, CON5.P$1, D5.CATHODE, L5.P$2
unnamed: CON5.P$2, D5.ANODE, Q5.P$5 (DRAIN), Q5.P$6 (DRAIN), Q5.P$7 (DRAIN), Q5.P$8 (DRAIN), Q5.P$9 (DRAIN), R21.P$1
unnamed: C19.P$1, R21.P$2
unnamed: C14.P$1, CON6.P$1, D6.CATHODE, L6.P$2
unnamed: CON6.P$2, D6.ANODE, Q6.P$5 (DRAIN), Q6.P$6 (DRAIN), Q6.P$7 (DRAIN), Q6.P$8 (DRAIN), Q6.P$9 (DRAIN), R22.P$1
unnamed: C20.P$1, R22.P$2
unnamed: C15.P$1, CON7.P$1, D7.CATHODE, L7.P$2
unnamed: CON7.P$2, D7.ANODE, Q7.P$5 (DRAIN), Q7.P$6 (DRAIN), Q7.P$7 (DRAIN), Q7.P$8 (DRAIN), Q7.P$9 (DRAIN), R23.P$1
unnamed: C21.P$1, R23.P$2
unnamed: C16.P$1, CON8.P$1, D8.CATHODE, L8.P$2
unnamed: CON8.P$2, D8.ANODE, Q8.P$5 (DRAIN), Q8.P$6 (DRAIN), Q8.P$7 (DRAIN), Q8.P$8 (DRAIN), Q8.P$9 (DRAIN), R24.P$1
unnamed: C22.P$1, R24.P$2
S5_G: Q5.P$4 (GATE), R17.P$1, U3.7 (OUTA)
S5_PWM: U3.2 (INA); also elsewhere on the board
S5_SENS_N: R25.P$2, R29.P$2; also elsewhere on the board
S5_SENS_P: C19.P$2, Q5.P$1 (SOURCE), Q5.P$2 (SOURCE), Q5.P$3 (SOURCE), R25.P$1; also elsewhere on the board
S6_G: Q6.P$4 (GATE), R18.P$1, U3.5 (OUTB)
S6_PWM: U3.4 (INB); also elsewhere on the board
S6_SENS_N: R26.P$2, R30.P$2; also elsewhere on the board
S6_SENS_P: C20.P$2, Q6.P$1 (SOURCE), Q6.P$2 (SOURCE), Q6.P$3 (SOURCE), R26.P$1; also elsewhere on the board
S7_G: Q7.P$4 (GATE), R19.P$1, U4.7 (OUTA)
S7_PWM: U4.2 (INA); also elsewhere on the board
S7_SENS_N: R27.P$2, R31.P$2; also elsewhere on the board
S7_SENS_P: C21.P$2, Q7.P$1 (SOURCE), Q7.P$2 (SOURCE), Q7.P$3 (SOURCE), R27.P$1; also elsewhere on the board
S8_G: Q8.P$4 (GATE), R20.P$1, U4.5 (OUTB)
S8_PWM: U4.4 (INB); also elsewhere on the board
S8_SENS_N: R28.P$2, R32.P$2; also elsewhere on the board
S8_SENS_P: C22.P$2, Q8.P$1 (SOURCE), Q8.P$2 (SOURCE), Q8.P$3 (SOURCE), R28.P$1; also elsewhere on the board
VB1: C17.P$1, C18.P$1, C23.P$1, C24.P$1, L5.P$1, L6.P$1, L7.P$1, L8.P$1, U3.1 (ENA), U3.6 (VDD), U3.8 (ENB), U4.1 (ENA), U4.6 (VDD), U4.8 (ENB); also elsewhere on the board

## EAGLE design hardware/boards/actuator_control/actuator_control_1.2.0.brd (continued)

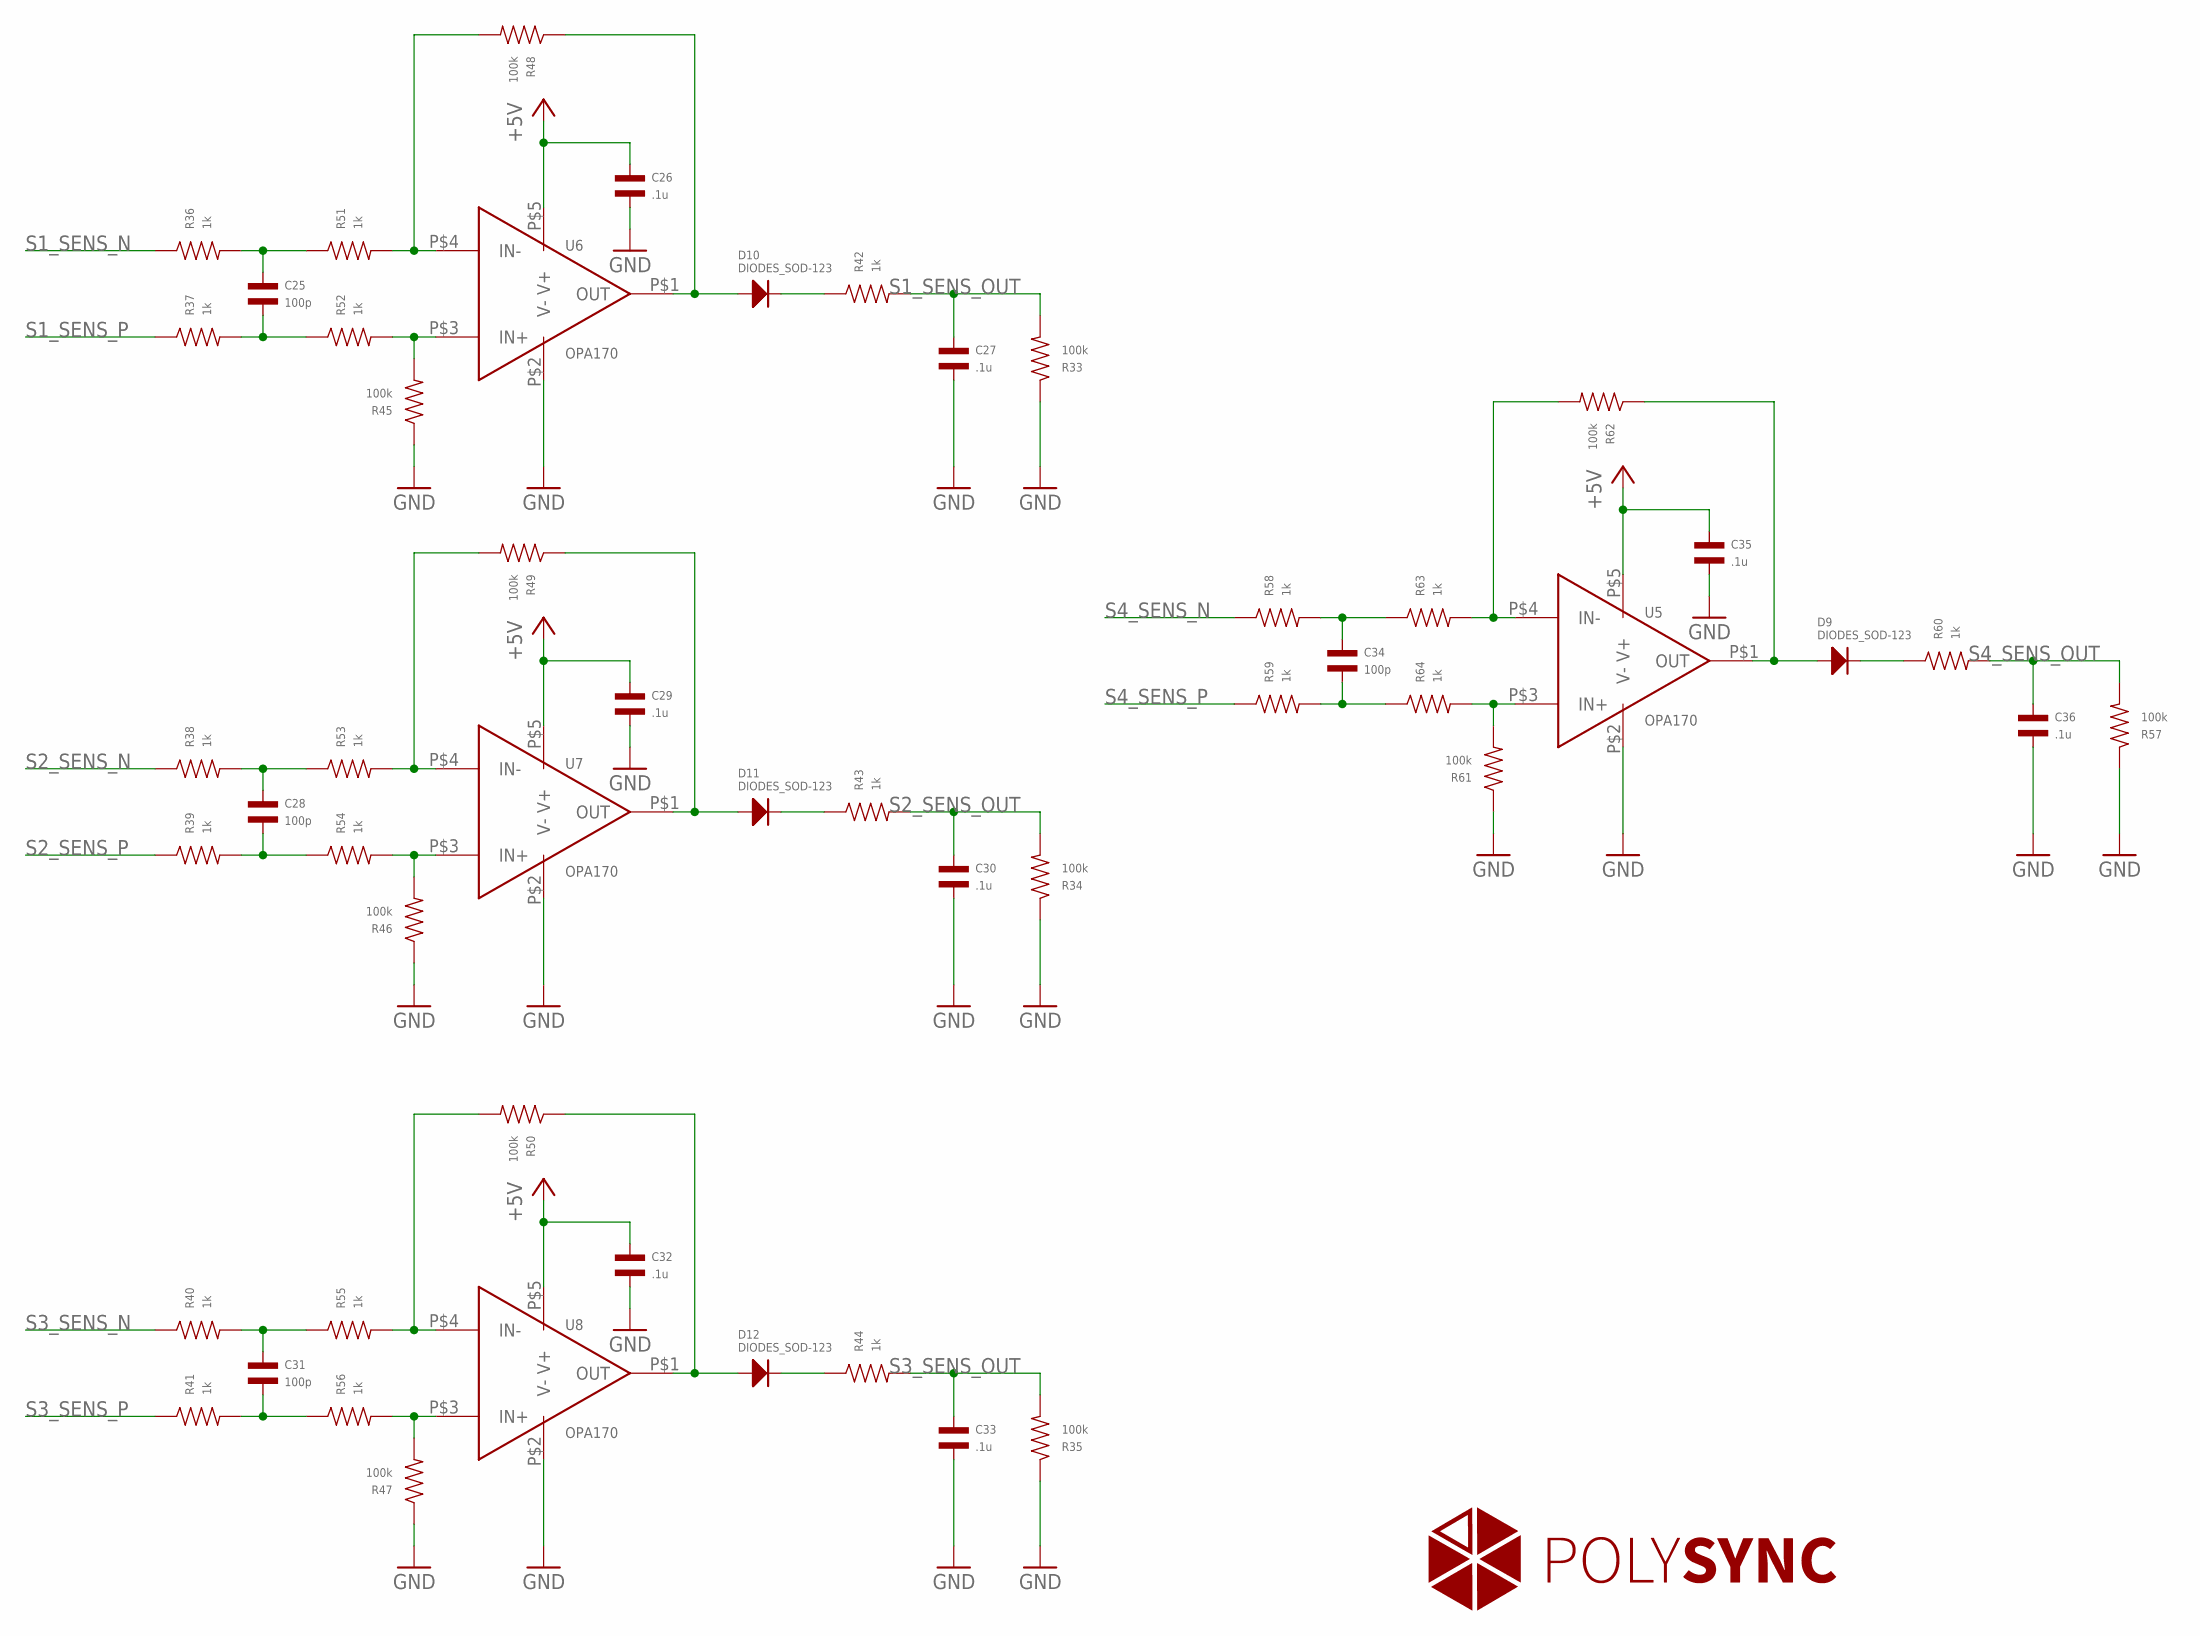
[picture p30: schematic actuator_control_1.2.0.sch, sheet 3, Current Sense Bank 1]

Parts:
C25, C28, C31, C34: 100p; C0402
C26, C27, C29, C30, C32, C33, C35, C36: .1u; C0402
D9, D10, D11, D12: DIODES_SOD-123; SOD-123
R33, R34, R35, R45, R46, R47, R48, R49, R50, R57, R61, R62: 100k; R0402
R36, R37, R38, R39, R40, R41, R42, R43, R44, R51, R52, R53, R54, R55, R56, R58, R59, R60, R63, R64: 1k; R0402
U5, U6, U7, U8: OPA170; SOT-23-5

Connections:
+5V: C26.P$1, C29.P$1, C32.P$1, C35.P$1, U5.P$5 (V+), U6.P$5 (V+), U7.P$5 (V+), U8.P$5 (V+); also elsewhere on the board
GND: C26.P$2, C27.P$2, C29.P$2, C30.P$2, C32.P$2, C33.P$2, C35.P$2, C36.P$2, R33.P$1, R34.P$1, R35.P$1, R45.P$1, R46.P$1, R47.P$1, R57.P$1, R61.P$1, U5.P$2 (V-), U6.P$2 (V-), U7.P$2 (V-), U8.P$2 (V-); also elsewhere on the board
unnamed: R48.P$2, R51.P$2, U6.P$4 (IN-)
unnamed: R45.P$2, R52.P$2, U6.P$3 (IN+)
unnamed: C25.P$2, R37.P$2, R52.P$1
unnamed: C25.P$1, R36.P$2, R51.P$1
unnamed: D10.ANODE, R48.P$1, U6.P$1 (OUT)
unnamed: D10.CATHODE, R42.P$1
unnamed: R49.P$2, R53.P$2, U7.P$4 (IN-)
unnamed: R46.P$2, R54.P$2, U7.P$3 (IN+)
unnamed: C28.P$2, R39.P$2, R54.P$1
unnamed: C28.P$1, R38.P$2, R53.P$1
unnamed: D11.ANODE, R49.P$1, U7.P$1 (OUT)
unnamed: D11.CATHODE, R43.P$1
unnamed: R50.P$2, R55.P$2, U8.P$4 (IN-)
unnamed: R47.P$2, R56.P$2, U8.P$3 (IN+)
unnamed: C31.P$2, R41.P$2, R56.P$1
unnamed: C31.P$1, R40.P$2, R55.P$1
unnamed: D12.ANODE, R50.P$1, U8.P$1 (OUT)
unnamed: D12.CATHODE, R44.P$1
unnamed: R62.P$2, R63.P$2, U5.P$4 (IN-)
unnamed: R61.P$2, R64.P$2, U5.P$3 (IN+)
unnamed: C34.P$2, R59.P$2, R64.P$1
unnamed: C34.P$1, R58.P$2, R63.P$1
unnamed: D9.ANODE, R62.P$1, U5.P$1 (OUT)
unnamed: D9.CATHODE, R60.P$1
S1_SENS_N: R36.P$1; also elsewhere on the board
S1_SENS_OUT: C27.P$1, R33.P$2, R42.P$2; also elsewhere on the board
S1_SENS_P: R37.P$1; also elsewhere on the board
S2_SENS_N: R38.P$1; also elsewhere on the board
S2_SENS_OUT: C30.P$1, R34.P$2, R43.P$2; also elsewhere on the board
S2_SENS_P: R39.P$1; also elsewhere on the board
S3_SENS_N: R40.P$1; also elsewhere on the board
S3_SENS_OUT: C33.P$1, R35.P$2, R44.P$2; also elsewhere on the board
S3_SENS_P: R41.P$1; also elsewhere on the board
S4_SENS_N: R58.P$1; also elsewhere on the board
S4_SENS_OUT: C36.P$1, R57.P$2, R60.P$2; also elsewhere on the board
S4_SENS_P: R59.P$1; also elsewhere on the board

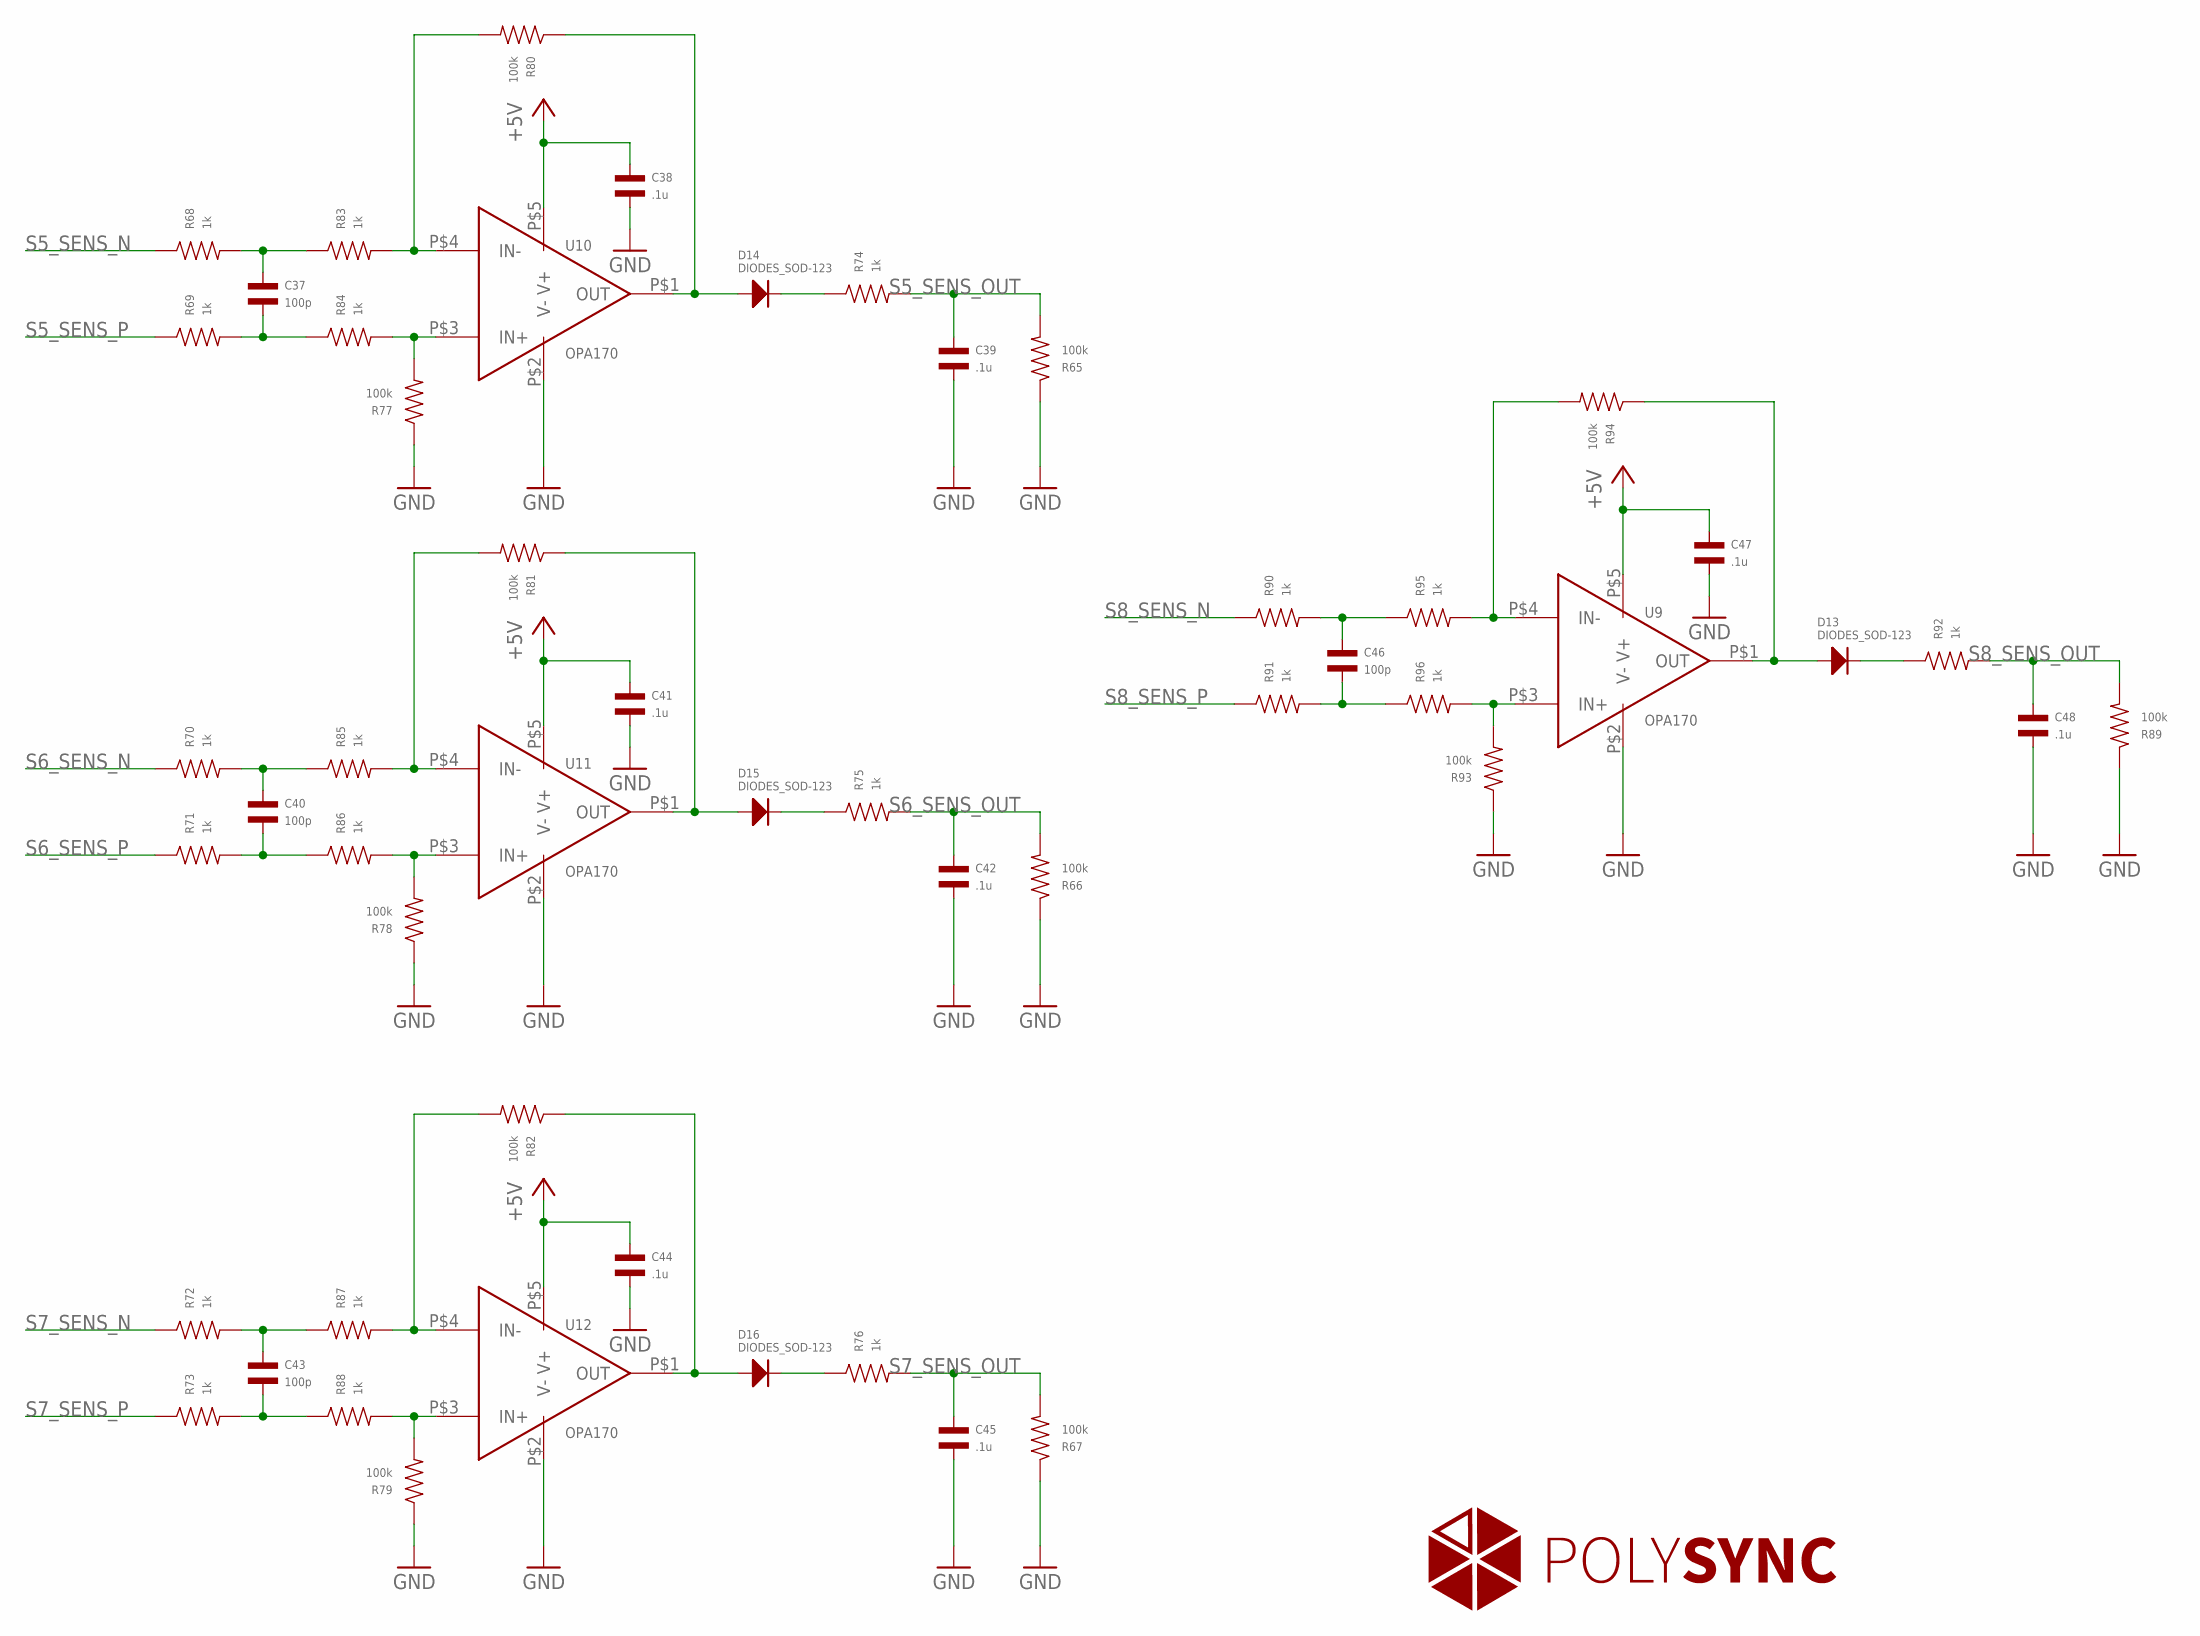
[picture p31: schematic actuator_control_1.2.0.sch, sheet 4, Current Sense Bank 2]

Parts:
C37, C40, C43, C46: 100p; C0402
C38, C39, C41, C42, C44, C45, C47, C48: .1u; C0402
D13, D14, D15, D16: DIODES_SOD-123; SOD-123
R65, R66, R67, R77, R78, R79, R80, R81, R82, R89, R93, R94: 100k; R0402
R68, R69, R70, R71, R72, R73, R74, R75, R76, R83, R84, R85, R86, R87, R88, R90, R91, R92, R95, R96: 1k; R0402
U9, U10, U11, U12: OPA170; SOT-23-5

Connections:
+5V: C38.P$1, C41.P$1, C44.P$1, C47.P$1, U9.P$5 (V+), U10.P$5 (V+), U11.P$5 (V+), U12.P$5 (V+); also elsewhere on the board
GND: C38.P$2, C39.P$2, C41.P$2, C42.P$2, C44.P$2, C45.P$2, C47.P$2, C48.P$2, R65.P$1, R66.P$1, R67.P$1, R77.P$1, R78.P$1, R79.P$1, R89.P$1, R93.P$1, U9.P$2 (V-), U10.P$2 (V-), U11.P$2 (V-), U12.P$2 (V-); also elsewhere on the board
unnamed: R80.P$2, R83.P$2, U10.P$4 (IN-)
unnamed: R77.P$2, R84.P$2, U10.P$3 (IN+)
unnamed: C37.P$2, R69.P$2, R84.P$1
unnamed: C37.P$1, R68.P$2, R83.P$1
unnamed: D14.ANODE, R80.P$1, U10.P$1 (OUT)
unnamed: D14.CATHODE, R74.P$1
unnamed: R81.P$2, R85.P$2, U11.P$4 (IN-)
unnamed: R78.P$2, R86.P$2, U11.P$3 (IN+)
unnamed: C40.P$2, R71.P$2, R86.P$1
unnamed: C40.P$1, R70.P$2, R85.P$1
unnamed: D15.ANODE, R81.P$1, U11.P$1 (OUT)
unnamed: D15.CATHODE, R75.P$1
unnamed: R82.P$2, R87.P$2, U12.P$4 (IN-)
unnamed: R79.P$2, R88.P$2, U12.P$3 (IN+)
unnamed: C43.P$2, R73.P$2, R88.P$1
unnamed: C43.P$1, R72.P$2, R87.P$1
unnamed: D16.ANODE, R82.P$1, U12.P$1 (OUT)
unnamed: D16.CATHODE, R76.P$1
unnamed: R94.P$2, R95.P$2, U9.P$4 (IN-)
unnamed: R93.P$2, R96.P$2, U9.P$3 (IN+)
unnamed: C46.P$2, R91.P$2, R96.P$1
unnamed: C46.P$1, R90.P$2, R95.P$1
unnamed: D13.ANODE, R94.P$1, U9.P$1 (OUT)
unnamed: D13.CATHODE, R92.P$1
S5_SENS_N: R68.P$1; also elsewhere on the board
S5_SENS_OUT: C39.P$1, R65.P$2, R74.P$2; also elsewhere on the board
S5_SENS_P: R69.P$1; also elsewhere on the board
S6_SENS_N: R70.P$1; also elsewhere on the board
S6_SENS_OUT: C42.P$1, R66.P$2, R75.P$2; also elsewhere on the board
S6_SENS_P: R71.P$1; also elsewhere on the board
S7_SENS_N: R72.P$1; also elsewhere on the board
S7_SENS_OUT: C45.P$1, R67.P$2, R76.P$2; also elsewhere on the board
S7_SENS_P: R73.P$1; also elsewhere on the board
S8_SENS_N: R90.P$1; also elsewhere on the board
S8_SENS_OUT: C48.P$1, R89.P$2, R92.P$2; also elsewhere on the board
S8_SENS_P: R91.P$1; also elsewhere on the board

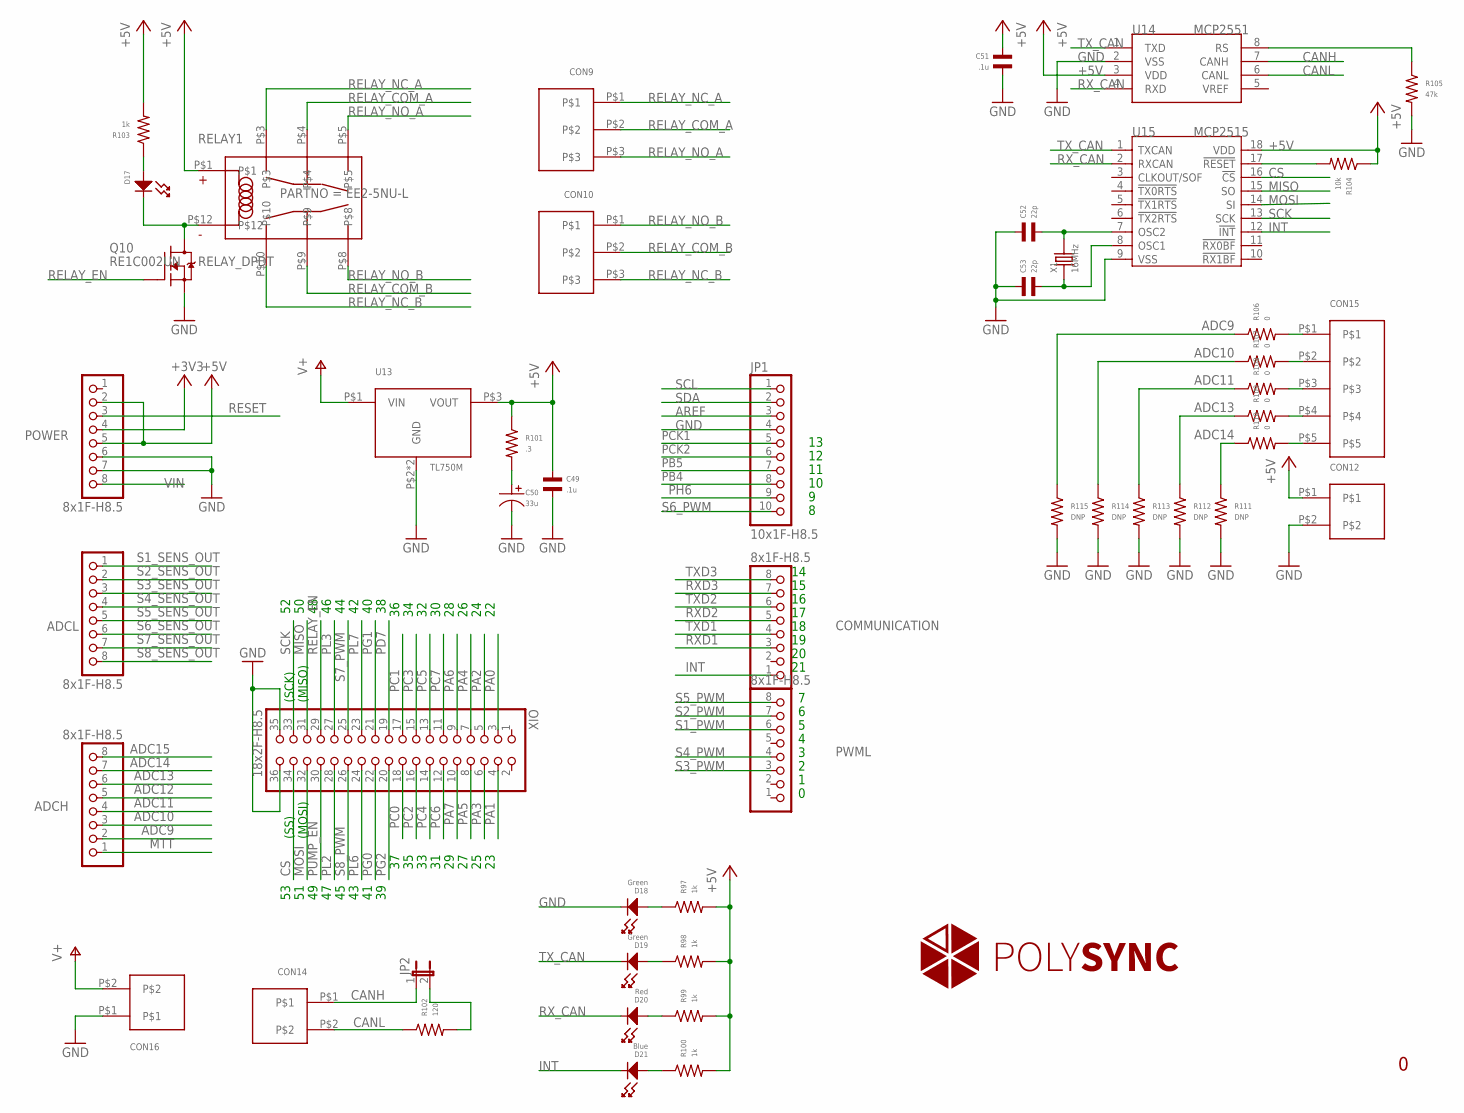
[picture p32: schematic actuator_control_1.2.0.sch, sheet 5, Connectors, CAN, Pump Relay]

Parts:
ADCH: 8x1F-H8.5; 1X08
ADCL: 8x1F-H8.5; 1X08
C49, C51: .1u; C0402
C50: 33u; CP1206
C52, C53: 22p; C0402
COMMUNICATION: 8x1F-H8.5; 1X08
CON9, CON10: CON3; PHOENIX_3_45
CON12, CON14: CON23.5MM; PHOENIX_2_45
CON15: CON5; PHOENIX_5_45
CON16: CON23.5MM; PHOENIX_2_45; PARTNO 1773976
D17: LED_SINGLE-0603; LED0603
D18, D19: Green; LED0603
D20: Red; LED0603
D21: Blue; LED0603
JP1: 10x1F-H8.5; 1X10
JP2: JP1E; JP1
POWER: 8x1F-H8.5; 1X08
PWML: 8x1F-H8.5; 1X08
Q10: RE1C002UN; EMT3F
R97, R98, R99, R100, R103: 1k; R0402
R101: .3; R0402
R102: 120; R0402
R104: 10k; R0402
R105: 47k; R0402
R106, R107, R108, R109, R110: 0; R0402
R111, R112, R113, R114, R115: DNP; R0402
RELAY1: RELAY_DPDT; KEMET_EE2; PARTNO EE2-5NU-L
U13: TL750M; TO-263
U14: MCP2551; SOIC8-6.0
U15: MCP2515; SOIC18
X1: 16MHz; HC49UP
XIO: 18x2F-H8.5; 2X18

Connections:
+3V3: POWER.4
+5V: C49.P$1, C51.P$1, CON12.P$1, POWER.2, POWER.5, R97.P$2, R98.P$2, R99.P$2, R100.P$2, R101.P$1, R103.P$2, R104.P$1, RELAY1.P$1, U13.P$3 (VOUT), U14.3 (VDD), U15.18 (VDD); also elsewhere on the board
ADC9: ADCH.2, R106.P$1, R115.P$1
ADC10: ADCH.3, R107.P$1, R114.P$1
ADC11: ADCH.4, R108.P$1, R113.P$1
ADC12: ADCH.5; also elsewhere on the board
ADC13: ADCH.6, R109.P$1, R112.P$1
ADC14: ADCH.7, R110.P$1, R111.P$1
ADC15: ADCH.8
AREF: JP1.3
CANH: CON14.P$1, JP2.1, U14.7 (CANH)
CANL: CON14.P$2, R102.P$1, U14.6 (CANL)
CS: U15.16 (!CS), XIO.34
GND: C49.P$2, C50.P$2, C51.P$2, C52.P$1, C53.P$1, CON12.P$2, CON16.P$1, D18.CATHODE, JP1.4, POWER.6, POWER.7, Q10.P$2 (S), R105.P$2, R111.P$2, R112.P$2, R113.P$2, R114.P$2, R115.P$2, U13.P$2 (GND), U13.P$4 (GND), U14.2 (VSS), U15.9 (VSS), XIO.35, XIO.36; also elsewhere on the board
INT: COMMUNICATION.1, D21.CATHODE, U15.12 (!INT)
MISO: U15.15 (SO), XIO.31
MOSI: U15.14 (SI), XIO.32
MTT: ADCH.1; also elsewhere on the board
unnamed: CON15.P$1, R106.P$2
unnamed: CON15.P$2, R107.P$2
unnamed: CON15.P$3, R108.P$2
unnamed: C52.P$2, U15.7 (OSC2), X1.2
unnamed: C53.P$2, U15.8 (OSC1), X1.1
unnamed: D17.CATHODE, Q10.P$3 (D), RELAY1.P$12
unnamed: D18.ANODE, R97.P$1
unnamed: D19.ANODE, R98.P$1
unnamed: D20.ANODE, R99.P$1
unnamed: D21.ANODE, R100.P$1
unnamed: R105.P$1, U14.8 (RS)
unnamed: D17.ANODE, R103.P$1
unnamed: CON15.P$4, R109.P$2
unnamed: CON15.P$5, R110.P$2
unnamed: C50.P$1, R101.P$2
unnamed: JP2.2, R102.P$2
PA0: XIO.3
PA1: XIO.4
PA2: XIO.5
PA3: XIO.6
PA4: XIO.7
PA5: XIO.8
PA6: XIO.9
PA7: XIO.10
PB4: JP1.8
PB5: JP1.7
PC0: XIO.18
PC1: XIO.17
PC2: XIO.16
PC3: XIO.15
PC4: XIO.14
PC5: XIO.13
PC6: XIO.12
PC7: XIO.11
PCK1: JP1.5; also elsewhere on the board
PCK2: JP1.6; also elsewhere on the board
PD7: XIO.19
PG0: XIO.22
PG1: XIO.21
PG2: XIO.20
PH6: JP1.9
PL2: XIO.28
PL3: XIO.27
PL6: XIO.24
PL7: XIO.23
PUMP_EN: XIO.30; also elsewhere on the board
RELAY_COM_A: CON9.P$2, RELAY1.P$4
RELAY_COM_B: CON10.P$2, RELAY1.P$9
RELAY_EN: Q10.P$1 (G), XIO.29
RELAY_NC_A: CON9.P$1, RELAY1.P$3
RELAY_NC_B: CON10.P$3, RELAY1.P$10
RELAY_NO_A: CON9.P$3, RELAY1.P$5
RELAY_NO_B: CON10.P$1, RELAY1.P$8
RESET: POWER.3
RST_N2: R104.P$2, U15.17 (!RESET)
RXD1: COMMUNICATION.3
RXD2: COMMUNICATION.5
RXD3: COMMUNICATION.7
RX_CAN: D20.CATHODE, U14.4 (RXD), U15.2 (RXCAN)
S1_PWM: PWML.6; also elsewhere on the board
S1_SENS_OUT: ADCL.1; also elsewhere on the board
S2_PWM: PWML.7; also elsewhere on the board
S2_SENS_OUT: ADCL.2; also elsewhere on the board
S3_PWM: PWML.3; also elsewhere on the board
S3_SENS_OUT: ADCL.3; also elsewhere on the board
S4_PWM: PWML.4; also elsewhere on the board
S4_SENS_OUT: ADCL.4; also elsewhere on the board
S5_PWM: PWML.8; also elsewhere on the board
S5_SENS_OUT: ADCL.5; also elsewhere on the board
S6_PWM: JP1.10; also elsewhere on the board
S6_SENS_OUT: ADCL.6; also elsewhere on the board
S7_PWM: XIO.25; also elsewhere on the board
S7_SENS_OUT: ADCL.7; also elsewhere on the board
S8_PWM: XIO.26; also elsewhere on the board
S8_SENS_OUT: ADCL.8; also elsewhere on the board
SCK: U15.13 (SCK), XIO.33
SCL: JP1.1
SDA: JP1.2
TXD1: COMMUNICATION.4
TXD2: COMMUNICATION.6
TXD3: COMMUNICATION.8
TX_CAN: D19.CATHODE, U14.1 (TXD), U15.1 (TXCAN)
V+: CON16.P$2, U13.P$1 (VIN); also elsewhere on the board
VIN: POWER.8

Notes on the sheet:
(SS)
(MOSI)
(SCK)
(MISO)

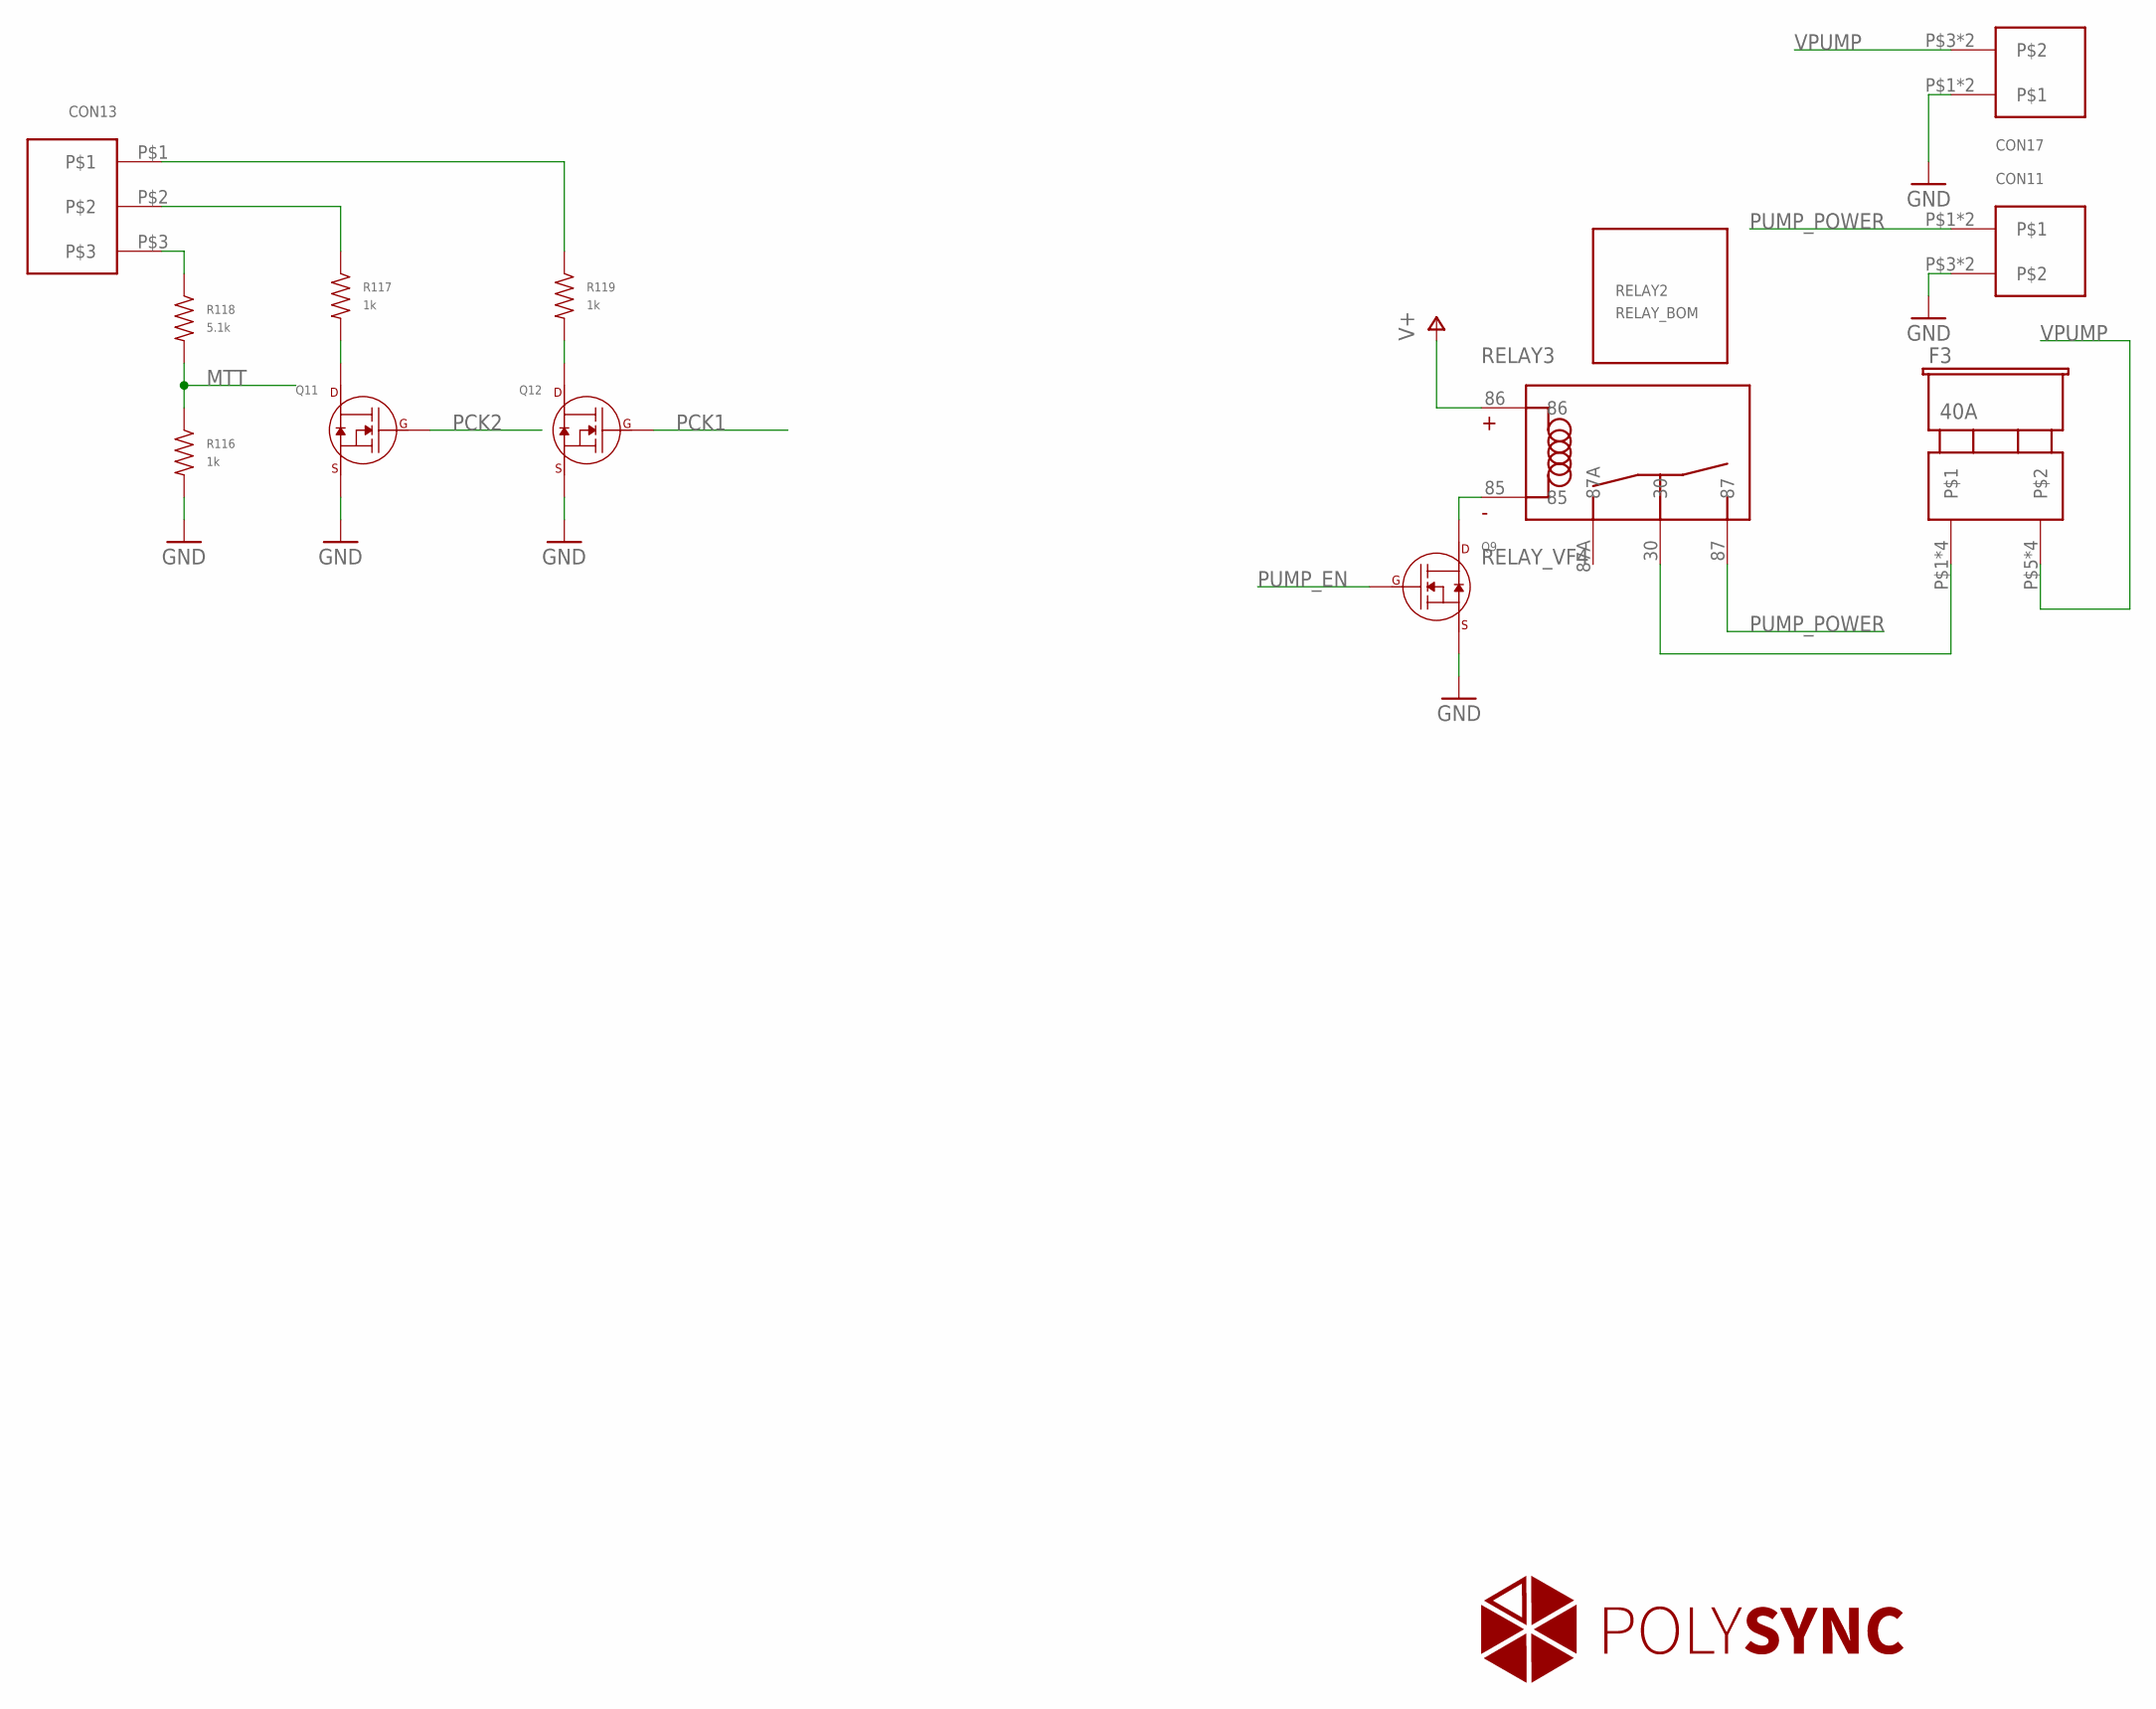
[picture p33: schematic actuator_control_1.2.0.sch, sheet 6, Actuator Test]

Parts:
CON11, CON17: CON210.16MM; PHOENIX_2_10.16MM; PARTNO 1773976
CON13: CON3; PHOENIX_3_45
F3: 40A; FUSE_ATO; PARTNO 178.6165.0001
Q9, Q11, Q12: N-CHANNEL_FET_SOT-23-3; SOT-23-3
R116, R117, R119: 1k; R0402
R118: 5.1k; R0402
RELAY2: RELAY_BOM; VCF4_RELAY; PARTNO 1432868-1
RELAY3: RELAY_VF4; VCF4-SOCKET; PARTNO VCF4-1000

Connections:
GND: CON11.P$3, CON11.P$4, CON17.P$1, CON17.P$2, Q9.P$2 (SOURCE), Q11.P$2 (SOURCE), Q12.P$2 (SOURCE), R116.P$2; also elsewhere on the board
MTT: R116.P$1, R118.P$2; also elsewhere on the board
unnamed: F3.P$1, F3.P$2, F3.P$3, F3.P$4, RELAY3.30
unnamed: Q9.P$3 (DRAIN), RELAY3.85
unnamed: CON13.P$3, R118.P$1
unnamed: CON13.P$2, R117.P$1
unnamed: CON13.P$1, R119.P$1
unnamed: Q11.P$3 (DRAIN), R117.P$2
unnamed: Q12.P$3 (DRAIN), R119.P$2
PCK1: Q12.P$1 (GATE); also elsewhere on the board
PCK2: Q11.P$1 (GATE); also elsewhere on the board
PUMP_EN: Q9.P$1 (GATE); also elsewhere on the board
PUMP_POWER: CON11.P$1, CON11.P$2, RELAY3.87
V+: RELAY3.86; also elsewhere on the board
VPUMP: CON17.P$3, CON17.P$4, F3.P$5, F3.P$6, F3.P$7, F3.P$8

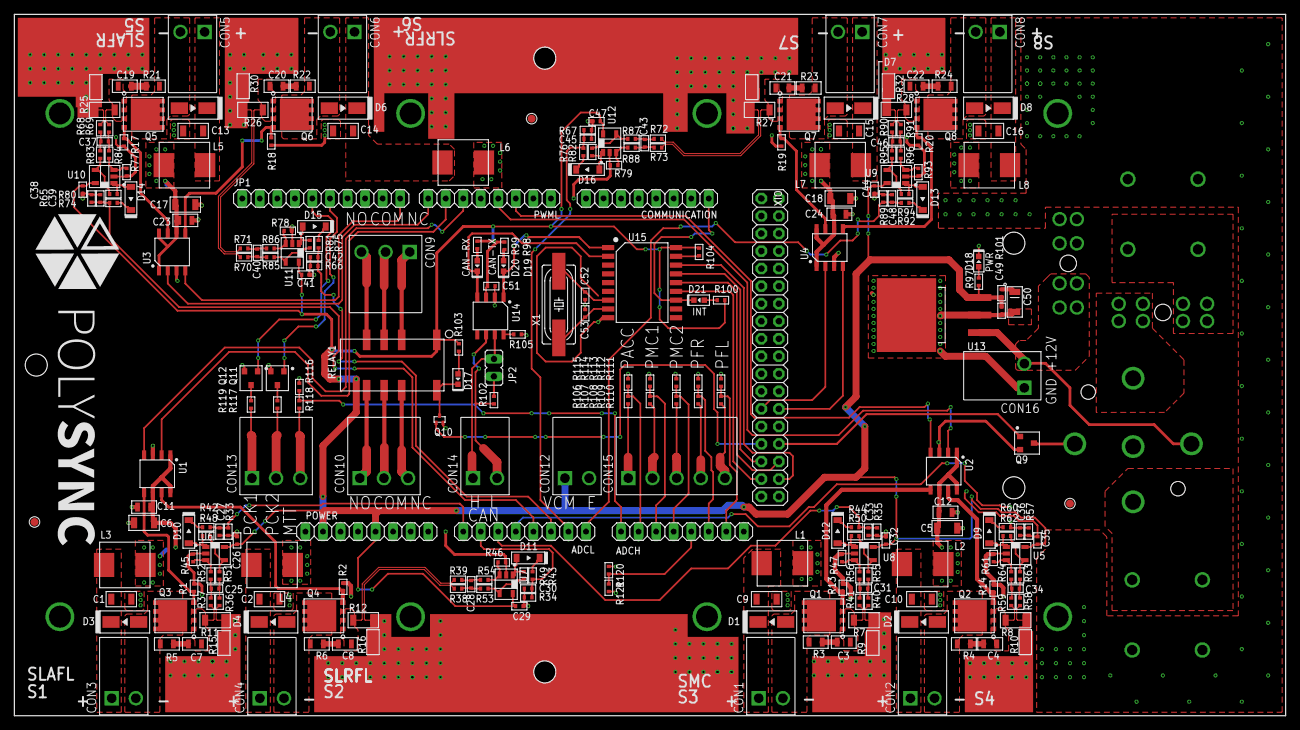
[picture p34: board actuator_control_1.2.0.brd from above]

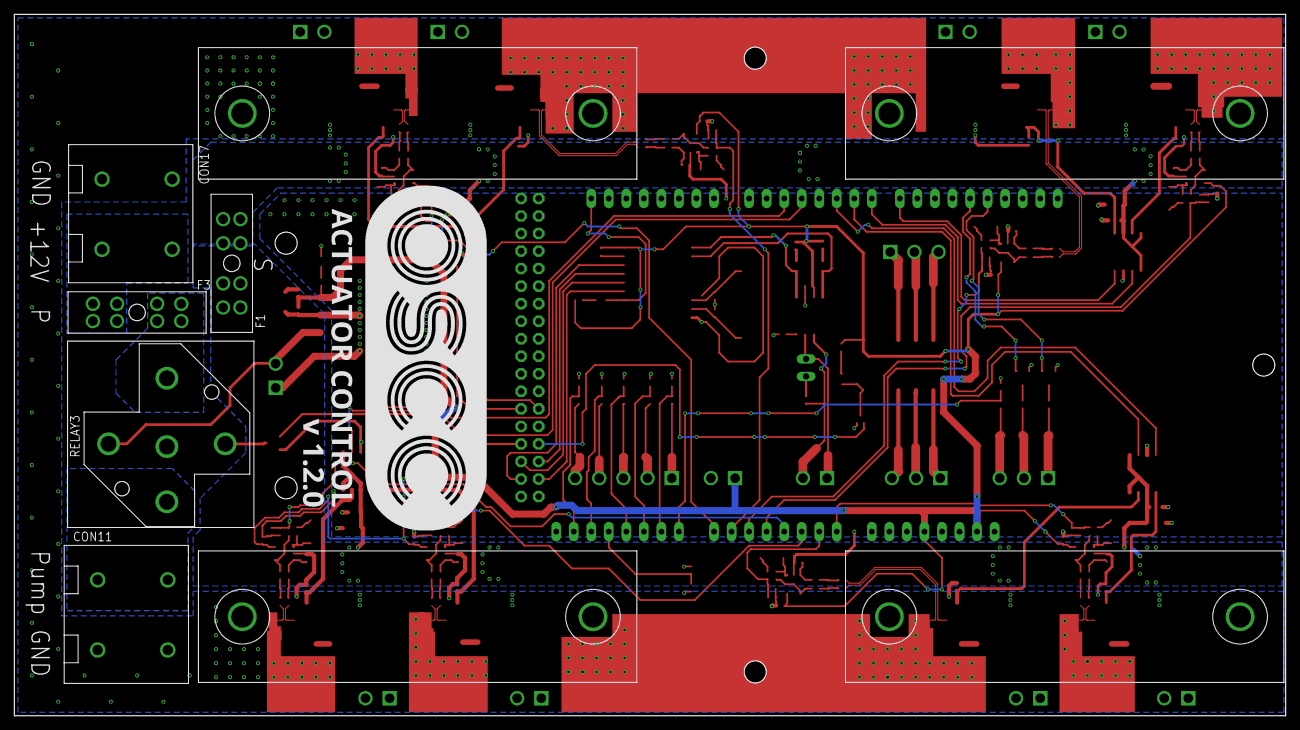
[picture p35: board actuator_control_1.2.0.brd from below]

Board: 2 copper layers, 184.2 x 101.6 mm, 270 parts (11 on the bottom side), 168 nets.

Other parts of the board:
U$3, U$7, U$9, U$10: HEATSINK_2X_75
U$11: POLYSYNC_ACT_1_2_0
U$13: POLYSYNC

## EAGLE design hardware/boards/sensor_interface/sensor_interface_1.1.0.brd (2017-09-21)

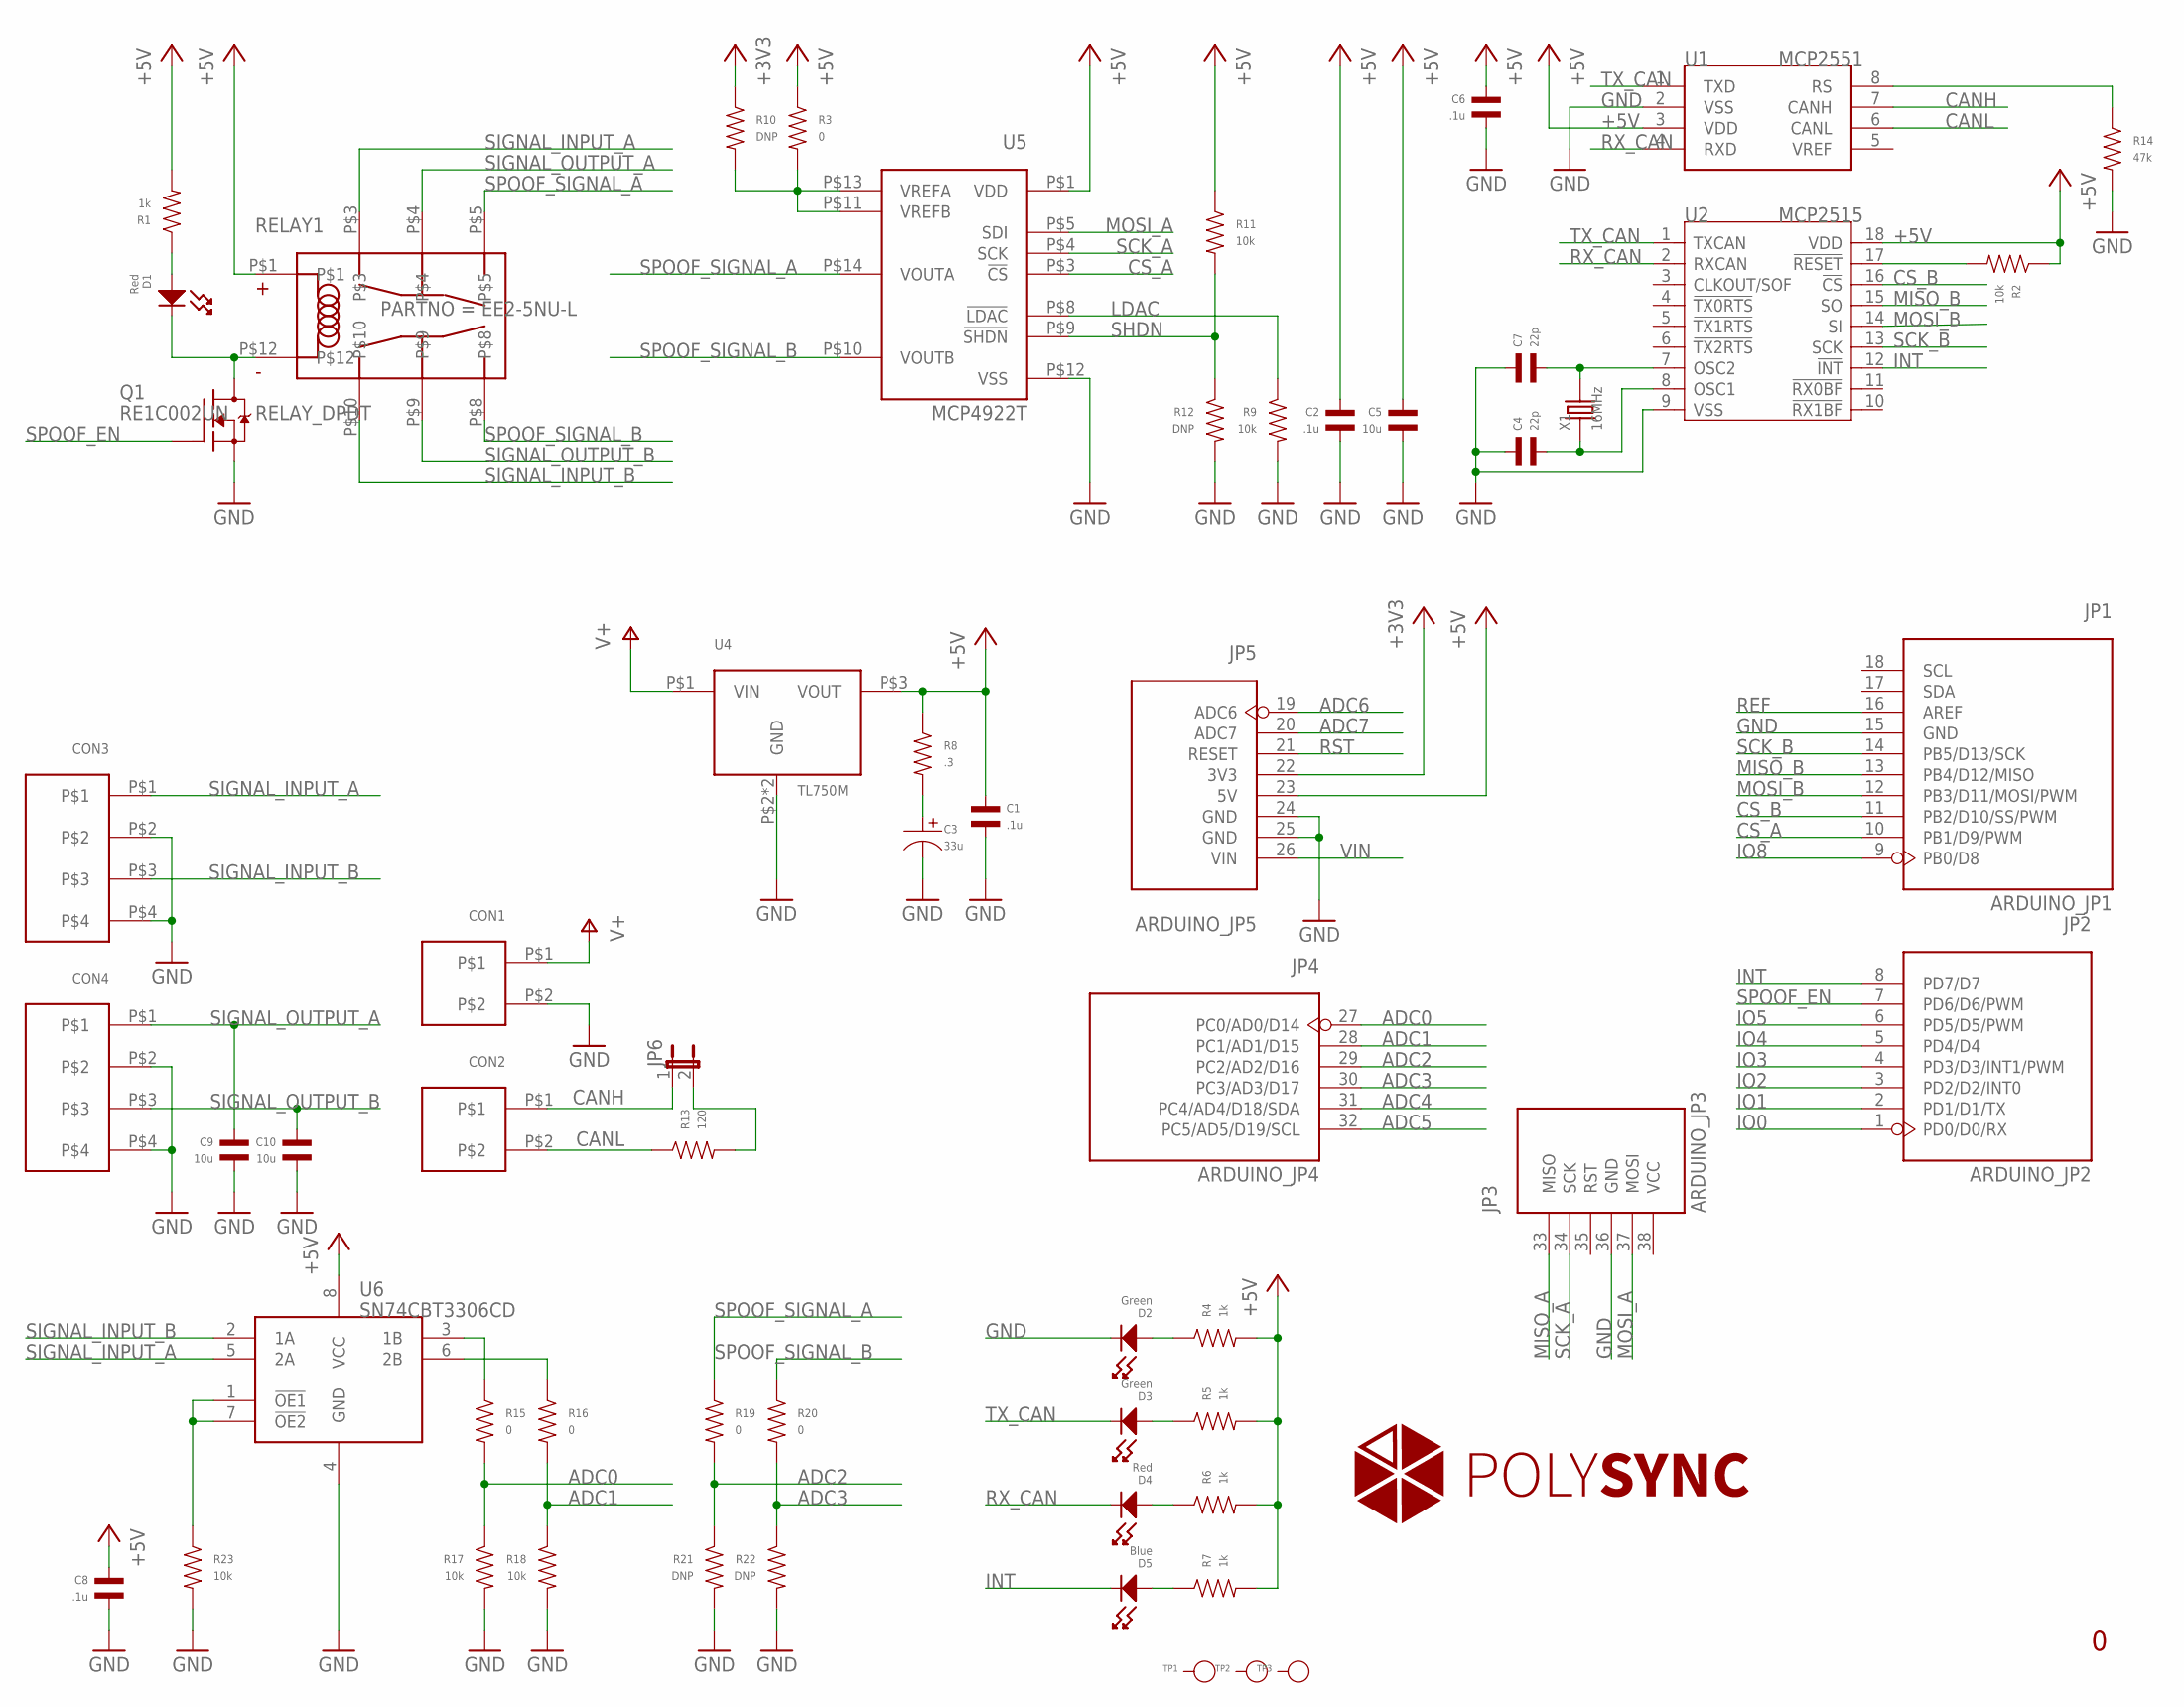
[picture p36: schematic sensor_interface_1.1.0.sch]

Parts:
C1, C2, C6, C8: .1u; C0402
C3: 33u; CP1206
C4, C7: 22p; C0402
C5, C9, C10: 10u; C0805
CON1, CON2: CON23.5MM; PHOENIX_2_45
CON3, CON4: CON4; PHOENIX_4_45
D1, D4: Red; LED0603
D2, D3: Green; LED0603
D5: Blue; LED0603
JP1: ARDUINO_JP1
JP2: ARDUINO_JP2
JP3: ARDUINO_JP3
JP4: ARDUINO_JP4
JP5: ARDUINO_JP5
JP6: JP1E; JP1
Q1: RE1C002UN; EMT3F
R1, R4, R5, R6, R7: 1k; R0402
R2, R9, R11, R17, R18, R23: 10k; R0402
R3, R15, R16, R19, R20: 0; R0402
R8: .3; R0402
R10, R12, R21, R22: DNP; R0402
R13: 120; R0402
R14: 47k; R0402
RELAY1: RELAY_DPDT; KEMET_EE2; PARTNO EE2-5NU-L
TP1, TP2, TP3: PAD-TEST-POINT'4545'; TP_4545
U1: MCP2551; SOIC8-6.0
U2: MCP2515; SOIC18
U4: TL750M; TO-263
U5: MCP4922T; TSSOP-14
U6: SN74CBT3306CD; SOIC-8
X1: 16MHz; HC49UP

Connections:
+3V3: JP5.22 (3V3), R10.P$1
+5V: C1.P$1, C2.P$1, C5.P$1, C6.P$1, C8.P$1, JP5.23 (5V), R1.P$2, R2.P$1, R3.P$1, R4.P$2, R5.P$2, R6.P$2, R7.P$2, R8.P$1, R11.P$1, RELAY1.P$1, U1.3 (VDD), U2.18 (VDD), U4.P$3 (VOUT), U5.P$1 (VDD), U6.8 (VCC)
ADC0: JP4.27 (PC0/AD0/D14), R15.P$2, R17.P$1
ADC1: JP4.28 (PC1/AD1/D15), R16.P$2, R18.P$1
ADC2: JP4.29 (PC2/AD2/D16), R19.P$2, R21.P$1
ADC3: JP4.30 (PC3/AD3/D17), R20.P$2, R22.P$1
ADC4: JP4.31 (PC4/AD4/D18/SDA)
ADC5: JP4.32 (PC5/AD5/D19/SCL)
ADC6: JP5.19 (ADC6)
ADC7: JP5.20 (ADC7)
CANH: CON2.P$1, JP6.1, U1.7 (CANH)
CANL: CON2.P$2, R13.P$1, U1.6 (CANL)
CS_A: JP1.10 (PB1/D9/PWM), U5.P$3 (!CS)
CS_B: JP1.11 (PB2/D10/SS/PWM), U2.16 (!CS)
GND: C1.P$2, C2.P$2, C3.P$2, C4.P$1, C5.P$2, C6.P$2, C7.P$1, C8.P$2, C9.P$2, C10.P$2, CON1.P$2, CON3.P$2, CON3.P$4, CON4.P$2, CON4.P$4, D2.CATHODE, JP1.15 (GND), JP3.36 (GND), JP5.24 (GND), JP5.25 (GND), Q1.P$2 (S), R9.P$2, R12.P$2, R14.P$2, R17.P$2, R18.P$2, R21.P$2, R22.P$2, R23.P$2, U1.2 (VSS), U2.9 (VSS), U4.P$2 (GND), U4.P$4 (GND), U5.P$12 (VSS), U6.4 (GND)
INT: D5.CATHODE, JP2.8 (PD7/D7), U2.12 (!INT)
IO0: JP2.1 (PD0/D0/RX)
IO1: JP2.2 (PD1/D1/TX)
IO2: JP2.3 (PD2/D2/INT0)
IO3: JP2.4 (PD3/D3/INT1/PWM)
IO4: JP2.5 (PD4/D4)
IO5: JP2.6 (PD5/D5/PWM)
IO8: JP1.9 (PB0/D8)
LDAC: R9.P$1, U5.P$8 (!LDAC)
MISO_A: JP3.33 (MISO)
MISO_B: JP1.13 (PB4/D12/MISO), U2.15 (SO)
MOSI_A: JP3.37 (MOSI), U5.P$5 (SDI)
MOSI_B: JP1.12 (PB3/D11/MOSI/PWM), U2.14 (SI)
unnamed: D3.ANODE, R5.P$1
unnamed: JP6.2, R13.P$2
unnamed: D1.CATHODE, Q1.P$3 (D), RELAY1.P$12
unnamed: C3.P$1, R8.P$2
unnamed: D4.ANODE, R6.P$1
unnamed: D2.ANODE, R4.P$1
unnamed: R3.P$2, R10.P$2, U5.P$11 (VREFB), U5.P$13 (VREFA)
unnamed: D5.ANODE, R7.P$1
unnamed: R14.P$1, U1.8 (RS)
unnamed: D1.ANODE, R1.P$1
unnamed: R23.P$1, U6.1 (!OE1), U6.7 (!OE2)
unnamed: R16.P$1, U6.6 (2B)
unnamed: R15.P$1, U6.3 (1B)
unnamed: C7.P$2, U2.7 (OSC2), X1.2
unnamed: C4.P$2, U2.8 (OSC1), X1.1
REF: JP1.16 (AREF)
RST: JP5.21 (RESET)
RST_N: R2.P$2, U2.17 (!RESET)
RX_CAN: D4.CATHODE, U1.4 (RXD), U2.2 (RXCAN)
SCK_A: JP3.34 (SCK), U5.P$4 (SCK)
SCK_B: JP1.14 (PB5/D13/SCK), U2.13 (SCK)
SHDN: R11.P$2, R12.P$1, U5.P$9 (!SHDN)
SIGNAL_INPUT_A: CON3.P$1, RELAY1.P$3, U6.5 (2A)
SIGNAL_INPUT_B: CON3.P$3, RELAY1.P$10, U6.2 (1A)
SIGNAL_OUTPUT_A: C9.P$1, CON4.P$1, RELAY1.P$4
SIGNAL_OUTPUT_B: C10.P$1, CON4.P$3, RELAY1.P$9
SPOOF_EN: JP2.7 (PD6/D6/PWM), Q1.P$1 (G)
SPOOF_SIGNAL_A: R19.P$1, RELAY1.P$5, U5.P$14 (VOUTA)
SPOOF_SIGNAL_B: R20.P$1, RELAY1.P$8, U5.P$10 (VOUTB)
TX_CAN: D3.CATHODE, U1.1 (TXD), U2.1 (TXCAN)
V+: CON1.P$1, U4.P$1 (VIN)
VIN: JP5.26 (VIN)

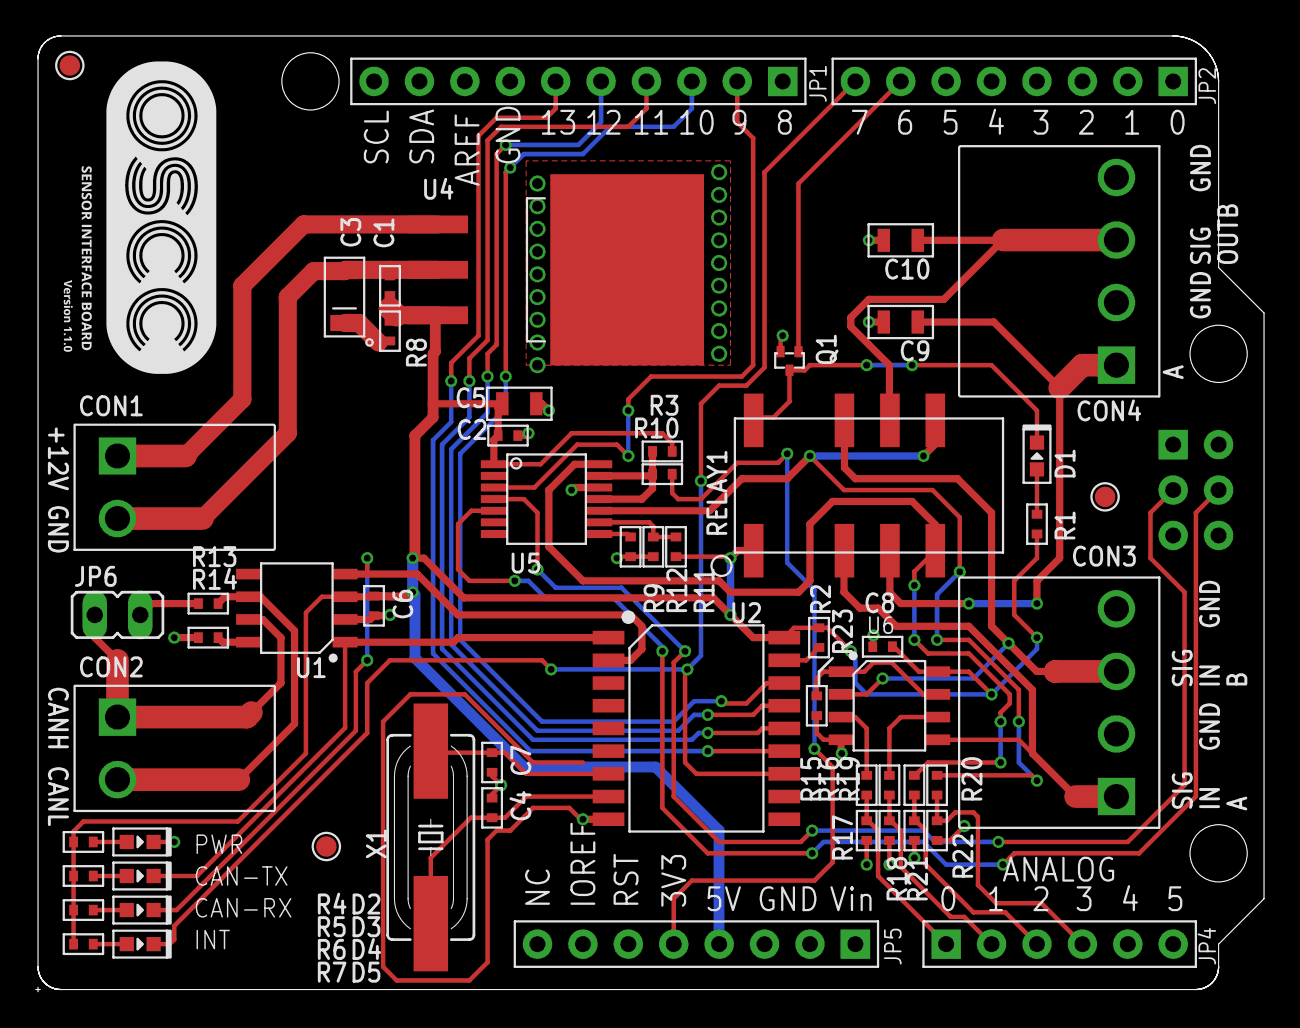
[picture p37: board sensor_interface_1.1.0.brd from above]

Board: 2 copper layers, 68.6 x 53.3 mm, 61 parts (0 on the bottom side), 45 nets.

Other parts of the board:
U$1: POLYSYNC_STEERING_BOT
U$2: POLYSYNC_SENSOR_1_1_0

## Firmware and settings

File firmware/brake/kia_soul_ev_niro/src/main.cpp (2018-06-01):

/**
 * @file main.cpp
 *
 */


#include "arduino_init.h"
#include "brake_control.h"
#include "communications.h"
#include "debug.h"
#include "init.h"


int main( void )
{
    init_arduino( );

    init_globals( );

    init_devices( );

    init_communication_interfaces( );

    start_timers( );

    DEBUG_PRINTLN( "init complete" );

    while( true )
    {
#ifdef __AVR_ATmega32U4__
        RXLED1;
#endif
        check_for_incoming_message( );

        check_for_faults( );
    }
}

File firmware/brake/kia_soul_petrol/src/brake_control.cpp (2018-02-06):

/**
 * @file brake_control.cpp
 *
 */


#include <Arduino.h>
#include <stdint.h>

#include "accumulator.h"
#include "brake_control.h"
#include "can_protocols/brake_can_protocol.h"
#include "communications.h"
#include "debug.h"
#include "dtc.h"
#include "globals.h"
#include "helper.h"
#include "master_cylinder.h"
#include "oscc_pid.h"
#include "vehicles.h"
#include "oscc_check.h"

/*
 * @brief Number of consecutive faults that can occur when reading the
 *        sensors before control is disabled.
 *
 */
#define SENSOR_VALIDITY_CHECK_FAULT_COUNT ( 4 )


static float read_pressure_sensor( void );
static void disable_brake_lights( void );
static void enable_brake_lights( void );
static bool check_master_cylinder_pressure_sensor_for_fault( void );
static bool check_accumulator_pressure_sensor_for_fault( void );
static bool check_wheel_pressure_sensor_for_fault( void );
static void startup_check( void );
static void pressure_startup_check( void );
static void pump_startup_check( void );


void set_accumulator_solenoid_duty_cycle( const uint16_t duty_cycle )
{
    cli();
    analogWrite( PIN_ACCUMULATOR_SOLENOID_FRONT_LEFT, duty_cycle );
    analogWrite( PIN_ACCUMULATOR_SOLENOID_FRONT_RIGHT, duty_cycle );
    sei();
}


void set_release_solenoid_duty_cycle( const uint16_t duty_cycle )
{
    cli();
    analogWrite( PIN_RELEASE_SOLENOID_FRONT_LEFT, duty_cycle );
    analogWrite( PIN_RELEASE_SOLENOID_FRONT_RIGHT, duty_cycle );
    sei();
}


void enable_control( void )
{
    if ( (g_brake_control_state.enabled == false)
         && (g_brake_control_state.operator_override == false)
         && (g_brake_control_state.startup_pressure_check_error == false)
         && (g_brake_control_state.startup_pump_motor_check_error== false) )
    {
        master_cylinder_close( );

        set_release_solenoid_duty_cycle( SOLENOID_PWM_OFF );

        g_brake_control_state.enabled = true;

        DEBUG_PRINTLN( "Control enabled" );
    }
}


void disable_control( void )
{
    if ( g_brake_control_state.enabled == true )
    {
        set_accumulator_solenoid_duty_cycle( SOLENOID_PWM_OFF );

        set_release_solenoid_duty_cycle( SOLENOID_PWM_ON );

        disable_brake_lights( );

        delay( 15 );

        master_cylinder_open( );

        set_release_solenoid_duty_cycle( SOLENOID_PWM_OFF );

        g_brake_control_state.enabled = false;

        DEBUG_PRINTLN( "Control disabled" );
    }
}


void check_for_operator_override( void )
{
    static condition_state_s operator_override_state = CONDITION_STATE_INIT;

    if( g_brake_control_state.enabled == true
        || g_brake_control_state.operator_override == true )
    {
        master_cylinder_pressure_s master_cylinder_pressure;

        master_cylinder_read_pressure( &master_cylinder_pressure );

        bool override_detected =
            ( master_cylinder_pressure.sensor_1_pressure >= BRAKE_OVERRIDE_PEDAL_THRESHOLD_IN_DECIBARS ) ||
            ( master_cylinder_pressure.sensor_2_pressure >= BRAKE_OVERRIDE_PEDAL_THRESHOLD_IN_DECIBARS );

        bool operator_overridden = condition_exceeded_duration(
                override_detected,
                FAULT_HYSTERESIS,
                &operator_override_state);

        if ( operator_overridden == true )
        {
            disable_control( );

            DTC_SET(
                g_brake_control_state.dtcs,
                OSCC_BRAKE_DTC_OPERATOR_OVERRIDE );

            publish_fault_report( );

            g_brake_control_state.operator_override = true;

            DEBUG_PRINTLN( "Operator override" );
        }
        else
        {
            DTC_CLEAR(
                g_brake_control_state.dtcs,
                OSCC_BRAKE_DTC_OPERATOR_OVERRIDE );

            g_brake_control_state.operator_override = false;
        }
    }
}


void check_for_sensor_faults( void )
{
    if ( (g_brake_control_state.enabled == true)
        || DTC_CHECK(g_brake_control_state.dtcs, OSCC_BRAKE_DTC_INVALID_SENSOR_VAL) )
    {
        bool master_cylinder_pressure_fault =
            check_master_cylinder_pressure_sensor_for_fault( );

        if( master_cylinder_pressure_fault == true )
        {
            DEBUG_PRINTLN( "Bad value read from master cylinder pressure sensor" );
        }


        bool accumulator_pressure_fault =
            check_accumulator_pressure_sensor_for_fault( );

        if( accumulator_pressure_fault == true )
        {
            DEBUG_PRINTLN( "Bad value read from accumulator pressure sensor" );
        }


        bool wheel_pressure_fault =
            check_wheel_pressure_sensor_for_fault( );

        if( wheel_pressure_fault == true )
        {
            DEBUG_PRINTLN( "Bad value read from wheel pressure sensor" );
        }


        if( (master_cylinder_pressure_fault == true)
            || (accumulator_pressure_fault == true)
            || (wheel_pressure_fault == true) )
        {
            disable_control( );

            DTC_SET(
                g_brake_control_state.dtcs,
                OSCC_BRAKE_DTC_INVALID_SENSOR_VAL );

            publish_fault_report( );
        }
        else
        {
            DTC_CLEAR(
                g_brake_control_state.dtcs,
                OSCC_BRAKE_DTC_INVALID_SENSOR_VAL );
        }
    }
}


void brake_init( void )
{
    cli();
    digitalWrite( PIN_ACCUMULATOR_SOLENOID_FRONT_LEFT, LOW );
    digitalWrite( PIN_ACCUMULATOR_SOLENOID_FRONT_RIGHT, LOW );
    digitalWrite( PIN_RELEASE_SOLENOID_FRONT_LEFT, LOW );
    digitalWrite( PIN_RELEASE_SOLENOID_FRONT_RIGHT, LOW );
    digitalWrite( PIN_WHEEL_PRESSURE_CHECK_1, LOW );
    digitalWrite( PIN_WHEEL_PRESSURE_CHECK_2, LOW );
    sei();

    pinMode( PIN_ACCUMULATOR_SOLENOID_FRONT_LEFT, OUTPUT );
    pinMode( PIN_ACCUMULATOR_SOLENOID_FRONT_RIGHT, OUTPUT );
    pinMode( PIN_RELEASE_SOLENOID_FRONT_LEFT, OUTPUT );
    pinMode( PIN_RELEASE_SOLENOID_FRONT_RIGHT, OUTPUT );
    pinMode( PIN_WHEEL_PRESSURE_CHECK_1, OUTPUT );
    pinMode( PIN_WHEEL_PRESSURE_CHECK_2, OUTPUT );

    set_release_solenoid_duty_cycle( SOLENOID_PWM_OFF );
    set_accumulator_solenoid_duty_cycle( SOLENOID_PWM_OFF );

    disable_brake_lights( );
    pinMode( PIN_BRAKE_LIGHT, OUTPUT );

#ifdef BRAKE_STARTUP_TEST
    startup_check( );
#endif
}
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

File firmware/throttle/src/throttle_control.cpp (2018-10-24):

/**
 * @file throttle_control.cpp
 *
 */


#include <Arduino.h>
#include <stdint.h>

#include "can_protocols/throttle_can_protocol.h"
#include "communications.h"
#include "debug.h"
#include "dtc.h"
#include "globals.h"
#include "oscc_dac.h"
#include "oscc_check.h"
#include "throttle_control.h"
#include "vehicles.h"


static void read_accelerator_position_sensor(
    accelerator_position_s * const value );


void check_for_faults( void )
{
    static condition_state_s grounded_fault_state = CONDITION_STATE_INIT;
    static condition_state_s operator_override_state = CONDITION_STATE_INIT;

    accelerator_position_s accelerator_position;

    if ( ( g_throttle_control_state.enabled == true )
        || (g_throttle_control_state.dtcs > 0) )
    {
        read_accelerator_position_sensor( &accelerator_position );

        uint32_t accelerator_position_average =
            (accelerator_position.low + accelerator_position.high) / 2;

        bool operator_overridden = condition_exceeded_duration(
                accelerator_position_average >= ACCELERATOR_OVERRIDE_THRESHOLD,
                FAULT_HYSTERESIS,
                &operator_override_state);

        bool inputs_grounded = check_voltage_grounded(
                accelerator_position.high,
                accelerator_position.low,
                FAULT_HYSTERESIS,
                &grounded_fault_state);

        // sensor pins tied to ground - a value of zero indicates disconnection
        if( inputs_grounded == true )
        {
            disable_control( );

            DTC_SET(
                g_throttle_control_state.dtcs,
                OSCC_THROTTLE_DTC_INVALID_SENSOR_VAL );

            publish_fault_report( );

            DEBUG_PRINTLN( "Bad value read from accelerator position sensor" );
        }
        else if ( operator_overridden == true )
        {
            disable_control( );

            DTC_SET(
                g_throttle_control_state.dtcs,
                OSCC_THROTTLE_DTC_OPERATOR_OVERRIDE );

            publish_fault_report( );

            g_throttle_control_state.operator_override = true;

            DEBUG_PRINTLN( "Operator override" );
        }
        else
        {
            g_throttle_control_state.dtcs = 0;

            if ( g_throttle_control_state.operator_override == true )
            {
                g_throttle_control_state.operator_override = false;
            }
        }
    }
}


void update_throttle(
    uint16_t spoof_command_high,
    uint16_t spoof_command_low )
{
    if ( g_throttle_control_state.enabled == true )
    {
        uint16_t spoof_high =
            constrain(
                spoof_command_high,
                THROTTLE_SPOOF_HIGH_SIGNAL_RANGE_MIN,
                THROTTLE_SPOOF_HIGH_SIGNAL_RANGE_MAX );

        uint16_t spoof_low =
            constrain(
                spoof_command_low,
                THROTTLE_SPOOF_LOW_SIGNAL_RANGE_MIN,
                THROTTLE_SPOOF_LOW_SIGNAL_RANGE_MAX );

        cli();
        g_dac.outputA( spoof_high );
        g_dac.outputB( spoof_low );
        sei();
    }
}


void enable_control( void )
{
    if( g_throttle_control_state.enabled == false
        && g_throttle_control_state.operator_override == false )
    {
        const uint16_t num_samples = 20;

        prevent_signal_discontinuity(
            g_dac,
            num_samples,
            PIN_ACCELERATOR_POSITION_SENSOR_LOW,
            PIN_ACCELERATOR_POSITION_SENSOR_HIGH );

        cli();
        digitalWrite( PIN_SPOOF_ENABLE, HIGH );
        sei();

        g_throttle_control_state.enabled = true;

        DEBUG_PRINTLN( "Control enabled" );
    }
}


void disable_control( void )
{
    if( g_throttle_control_state.enabled == true )
    {
        const uint16_t num_samples = 20;

        prevent_signal_discontinuity(
            g_dac,
            num_samples,
            PIN_ACCELERATOR_POSITION_SENSOR_LOW,
            PIN_ACCELERATOR_POSITION_SENSOR_HIGH );

        cli();
        digitalWrite( PIN_SPOOF_ENABLE, LOW );
        sei();

        g_throttle_control_state.enabled = false;

        DEBUG_PRINTLN( "Control disabled" );
    }
}


static void read_accelerator_position_sensor(
    accelerator_position_s * const value )
{
    cli();
    value->high = analogRead( PIN_ACCELERATOR_POSITION_SENSOR_HIGH );
    value->low = analogRead( PIN_ACCELERATOR_POSITION_SENSOR_LOW );
    sei();
}

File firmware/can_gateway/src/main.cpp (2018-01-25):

/**
 * @file main.cpp
 *
 */


#include <avr/wdt.h>

#include "arduino_init.h"
#include "communications.h"
#include "debug.h"
#include "init.h"
#include "timer.h"


int main( void )
{
    init_arduino( );

    init_globals( );

    init_communication_interfaces( );

    start_timer( );

    wdt_enable( WDTO_250MS );

    DEBUG_PRINTLN( "init complete" );

    while( true )
    {
        wdt_reset();

        check_for_module_reports( );

        republish_obd_frames_to_control_can_bus( );
    }
}

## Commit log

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2016-11-30 Add tests (#11)
    * started work on tests plans and test firmware
    * added test plan for steering, throttle
    * added brake board tests
    * add steering/throttle DAC and CAN tests
    * add CAN module tests
    * minor tweaks
    * added steering tests, fixed DAC tests for steering/throttle
    * fixed executable issue in branch
    * added brake actuator assy
    * added test functions to test firmware
    * Fix broken list order in brake controller markdown
    * Fix broken list order in steering controller md
    * Fix broken list order in throttle controller md
    * changed bench test to test up to 100% duty cylce
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2016-12-30 Update images and models (#18)
    * Add steering, throttle and brake schematic files
    * Add the schematics for both boards to the repo. This commit only contains PDF version of the brake board schematic
    ** Finishing up routing before adding the remaining filetypes for the brake board
    * Updated enclosure lid to have proper tolerances for SLA printing
    * Created images for connectors and updated overview image
    * Fixed misnamed files
    [EStopHousing.SLDPRT, EStopHousing.STL, STC_lid.SLDPRT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]
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2017-01-01 Style fixes
    Remove outdated and confusing comments. Add comments on things I found
    confusing.
    Replace hard-coded 0.48 and 0.2 with ZERO_PRESSURE and PRESSURE_STEP,
    respectively.
    Fix messed up #define of PSYNC_DEBUG_FLAG.
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2017-01-11 Add exception handling for build failure (#30)
    Prior to this commit, we did not have exception handling in place
    for build failures. This meant that the workspace was not getting
    properly cleaned up on a failed build, so the build machines' storage
    was getting clogged with workspaces from failed builds. This
    commit adds exception handling so that if the build fails in the
    checkout or build stage, the workspace will be deleted.
2017-01-12 Properly set DAC for control boards (#29)
    * Prior to this commit the code set the prototype style DACs.
    This commit updates the codes to properly set the DACs on the OSCC
    boards. This code also has more consistent varaible naming.
    * update method of seting dac in steering code
    * Fixed naming collision between Kia C CAN messages and
    OSCC Control CAN messages.
    Fixed CAN CS pin numbering on OSCC sensor boards.
    Fixed debug logging output.
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2017-01-17 Prior to this commit, there were no ADC/DAC Diagnostic tests for the OSCC Throttle Module. After this commit, the framework for such a test will exist. Currently, the check_spoof_voltage( ) function 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
2017-01-18 Add style changes and type casting Prior to this commit a couple files did not include a newline at the end of the file. In addition to this the uint_8 override field of the incoming messages was bei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
2017-01-18 Prior to this commit, a discrepancy between high and low spoof signals existed. After this commit, the cause of the issue has been determined as a wiring issue to either the ADC or from the DAC. This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
2017-01-19 Bugfix/add common h (#38)
    * Add common.h file and update dependancies
    Prior to this commit various macros were duplicated in the steering, throttle, break and obd_can firmware. This commit adds a high level common.h file and moves these duplicate macros to this common location. It also renames can_gateway.io which was misspelled.
    * Update common.h dependancies for tests
    Prior to this the test files in this project used their own local macros instead of the ones defined in common.h. This commit removes those local macros and replaces them with an include from common.h.
    * Add common.h file
    Prior to this commit, the common.h file which holds common macros in multiple firmware files, di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
2017-01-20 Prior to this commit, the DAC/ADC Diagnostics were in a debug state due to a voltage anomaly. After this commit, the voltage issue is solved, debug prints are removed, and the test is in line and rea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
2017-01-20 Standardize the PID library (#42)
    * Remove PIDV1c library from throttle control
    Prior to this commit the PIDV1 library was unneccessairly included in the throttle control code. It is not used so is now removed.
    * Move new PID library, remove old PID library
    Prior to this commit the custom PID library, used in the steering controller, was located in the steering controller directory. This commit moves it to the arduino_libraries directory so that it can be referenced by multiple firmware projects. In addition, the PIDv1 library was removed so that it could be replaced with the new custom library.
    * Add safety check for pid_update calculation
    Prior to this commit there was no checking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
2017-01-23 Prior to this commit, the voltage threshold for the ADC/DAC Diagnostics on the throttle board were too tight and flagged an error when another board (brake) was tested. After this commit, the voltage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
2017-01-23 Prior to this commit, there was no DAC/ADC Diagnostics for the steering module. After this commit, there will be such a test. The failure threshold is set at 200mV and is ready to be tested.
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2017-01-24 Prior to this commit, the word "break" was incorrectly used instead of "brake". After this commit, this is corrected. Care was taken to not replace any break commands in code.
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2017-01-25 Rename variable with incorrect spelling
    Prior to this commit, there was a misnamed variable referenced in the
    brake firmware and brake test code. This commit fixes the incorrect
    spelling of the variable, and updates the firmware and firmware test
    usage to use the correct variable.
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2017-01-26 Add smoother control of steering, brake (#55)
    * Add smoother control of steering, brake
    Prior to this commit steering, throttle and brake control didn't have any filtering of their respective setpoints. Further, steering lacked the functionality to smooth control via dynamically changing the max steering rate. This commit adds the functionality to smooth steering and brake through exponential filtering. It also adds the functionality to smooth throttle control through filtering, but does not implement this (as it was not neccessary). Finally it adds dynamic control of the max steering wheel rate, which further smooths out control.
    * Add style changes
    Prior to this commit there were a co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
2017-01-27 Refactor to conform to coding standards
    Prior to this commit, the code in the brake module did not conform to
    the coding standards in contributing.md. This commit corrects some of
    those issues to bring it closer to conforming to the standard. These
    edits are not complete and there is still further work to be done.
2017-01-27 Add correct factor for steering max velocity Prior to this commit the multiplication factor for the steering wheel max velocity field was too low. This commit adds the correct multiplication factor.
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2017-01-27 Fix the brake bench tests incorrect pin number
    Prior to this commit, the brake bench test was referencing the
    prototype hardware (V0.9) pin number for the accumulator pump motor.
    This commit sets the correct accumulator pump pin number according to the V1 hardware
    schematics defined here:
    https://github.com/PolySync/OSCC/blob/devel/boards/actuator_control_board/actuator_control_board_sch_1.0.0.pdf
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2017-01-27 Add example of an if statement format (#56)
    * Add example of an if statement format
    * Fix formatting and numbering errors
    Fixed numerous formatting and numbering errors in the text.
    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
2017-01-30 Fix the steering output pins (#61)
    Prior to this commit the output pins in the steering controller module were swapped for the new boards. This commit corrects these pins.
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2017-01-31 Prior to this commit the system overview diagram did not show the correct wiring for the 12 volt power system and showed ground connections which are not necessary. This commit fixes those issues and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
2017-02-02 Prior to this commit the colors of the wires for the pressure sensors in the system diagram did not match the colors of the wires in the prius wiring diagram. This commit fixes the colors so that the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
2017-02-03 Prior to this commit, the steering VOLTAGE_THRESHOLD was incorrectly set to 200V. This commit corrects this typo, setting it to the correct value of 0.096V. Also, "THRESH" is replaced with "THRESHOLD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
2017-02-06 Add driver override to steering module Prior to this commit we didn't have a good way of disabling on driver override on steering wheel. This commit adds the functionality to detect a driver override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
2017-02-07 Fix timeout steering command CAN message RX
    Prior to this commit the timeout for receiving steering command was too large. This commit changes this timeout to a reasonable value.
2017-02-07 Prior to this commit e-stop power colors were wrong and the brake pedal switch has a misleading color. This commit fixes those issues.
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2017-04-21 Rename torque struct to accel struct
    Prior to this commit, the throttle firmware had references to "torque"
    which is a copy-paste error from the steering firmware. This commit
    replace the references to "torque" with "accel", because the throttle
    module spoofs a pedal position, not steering wheel torque.
    [throttle_control.cpp]
2017-04-21 Replace doubles with floats
    Prior to this commit, doubles were being used when a float would be
    sufficient. While a float and a double on ATmega-based Arduinos are
    are identical (4 bytes), they may not be elsewhere. This commit changes
    all doubles to floats in an attempt at future portability.
    [release_pressure.ino]
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2017-05-02 Replace magic numbers with descriptive macros
    [brake_control.cpp, globals.h, steering_control.cpp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]
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2017-05-24 Reset brake system to known state at module init
    [init.cpp]
2017-05-26 Check for OBD timeout and disable if one occurs
    Prior to this commit, the steering and brake modules did not check for
    an OBD timeout which allowed them to operate as if they were receiving
    OBD information (required for their feedback systems to work correctly)
    when they in fact were making control decisions on invalid information.
    This commit adds checks for the validity of the data that the modules
    receive from the Chassis State 1 report (sent from the CAN gateway)
    before using the data, and keeps a timeout tracker of when they receive
    valid data. If valid data is not received after a certain amount of
    time, they disable and set a new OBD timeout fault in their report messages,
    which is ch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
    [brake_control.cpp, globals.h, init.cpp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]
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2017-06-01 Fix broken signal smooth header references
    [accumulator.cpp, brake_control.cpp, master_cylinder.cpp]
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2017-06-08 Check throttle sensors for valid values
    Prior to this commit, the sensors used in the throttle module (i.e.,
    accelerator position sensor) were not checked for valid values so it was
    possible for a sensor wire to become disconnected while control
    continued to be enabled. This commit does a periodic check of the sensor
    values to see if any of them return a value of 0 indicating a problem
    because the sensor pins are tied to ground and will be 0 if they're
    disconnected.
    [globals.h, init.cpp, main.cpp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]
2017-06-09 Check brake sensors for valid values
    Prior to this commit, the sensors used in the brake module
    (i.e., accumulator pressure sensor, master cylinder pressure
    sensor, wheel pressure sensor) were not checked for valid values
    so it was possible for a sensor wire to become disconnected while
    control continued to be enabled. This commit does a periodic check
    of the sensor values to see if any of them return a value of 0
    indicating a problem because the sensor pins are tied to ground
    and will be 0 if they're disconnected.
    [brake_control.cpp, globals.h, main.cpp]
2017-06-09 Check steering sensors for valid values
    Prior to this commit, the sensors used in the steering module (i.e.,
    torque sensor) were not checked for valid values so it was
    continued to be enabled. This commit does a periodic check of the
    sensor values to see if any of them return a value of 0 indicating a
    problem because the sensor pins are tied to ground and will be 0 if
    they're disconnected.
    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
    [globals.h, main.cpp, steering_control.cpp]
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2017-07-12 Remove exponential filters on sensor reads
    Prior to this commit, there were exponential filters when reading from
    vehicle sensors because there was a lot of noise from the brake
    actuator, but now the brake actuator is much less noisy and exponential
    filters are unnecessary. This commit removes the exponential filters
    from the modules.
    [accumulator.cpp, brake_control.cpp, master_cylinder.cpp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]
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2017-07-17 Use timer for throttle fault checking
    Prior to this commit, the throttle module used timestamps to keep track
    of when to check for faults and when timeouts occurred. This commit
    replaces the timestamp system with a timer system where faults are
    checked ten times a second. For command timeouts, a flag is cleared
    every time a command is received and set at the end of the interrupt
    service routine - if a command is not received between one ISR call and
    the next (a span of 100ms), then the timeout flag has not been cleared
    and a timeout is considered to have occurred. For sensor validity
    checks, they are run once with every ISR call, meaning they're run every
    100ms.
    [globals.h, init.cpp, main.cpp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]
2017-07-17 Use timer for steering fault checking
    Prior to this commit, the steering module used timestamps to keep track
    checks, they are run once with every ISR call, meaning they're run
    every 100ms.
    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
    [globals.h, init.cpp, main.cpp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]
2017-07-17 Use timer for brake fault checking
    Prior to this commit, the brake module used timestamps to keep track
    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
    [brake_control.cpp, globals.h, init.cpp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]
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2017-07-20 Disable interrupts during CAN operations
    Prior to this commit, the timers were interrupting during CAN Tx and Rx
    operations, causing corrupted CAN frames and the CAN library getting
    stuck in limbo. This commit adds cli()/sei() blocks around CAN
    operations so that they can execute atomically.
    [globals.h, init.cpp, main.cpp]
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2017-07-25 Fix brake build error
    [init.cpp]
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2017-07-27 Fix disabled signal reads
    Prior to this commit, I accidentally left bench test junk in the firmware and committed it. The horror! This commit changes it back to the way it's supposed to be/
    [steering_control.cpp]
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2017-07-28 Remove Kia Soul references from the firmware
    Prior to this commit, the firmware had a concept of what vehicle it was
    building for which is no longer in line with the way the software stack
    is architected (i.e., firmware should be consistent across vehicles, all
    that changes is inside of the vehicle specific header like
    "kia_soul.h"). This commit removes the KIA Soul references and keeps the
    firmware vehicle agnostic.
    [accumulator.cpp, brake_control.cpp, globals.h]
2017-07-28 Disable interrupts when interfacing with hardware
    Prior to this commit, the timers would interrupt the modules while they
    were talking to the hardware which caused sporadic issues. This commit
    disable interrupts whenever the firmware is interfacing with a piece of
    hardware (CAN, sensors, solenoids, etc).
    [accumulator.cpp, brake_control.cpp, init.cpp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]
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2017-08-01 Add patch for legacy actuator board support
    Prior to this commit, the new firmware would not work on older (< 1.1.0) versions of the actuator control board due to new startup tests that use new pins. This commit adds a CMake option to allow legacy board users to disable these startup checks, allowing them to still use the firmware as usual. It also updates the README to reflect these changes.
    [brake_control.cpp]
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2017-08-17 Replace display timeout checking with timer
    [main.cpp]
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2017-08-24 Update operator override
    Prior to this commit, the previous methodology for detecting operator override was no longer sufficient to allow for using the new expanded range of possible spoofed outputs.
    This commit updates the previous method from reading a specific value from the torque sensor to instead detect large amounts of torque over a period of time.
    [steering_control.cpp]
2017-08-25 Update exponential filter for steering control
    Prior to this commit, the inputs from the sensor read wasn't being smoothed out enough to account for noise at the mechanical limits of the steering wheel. This commit applies stronger smoothing, making it easier to detect operator override.
    [steering_control.cpp]
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2017-08-25 Code cleanup
    Prior to this commit, the code was working but didn't fit the style guide. This commit updates it to better adhere to the style guidelines.
    [steering_control.cpp]
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2017-08-31 Disable interrupts around analog functions
    Prior to this commit, there were three spots in the Kia Soul brake
    firmware that were not disabling interrupts before interacting with the
    hardware which caused intermittent problems. This commit adds the cli()
    and sei() calls around the critical sections.
    [brake_control.cpp]
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2017-09-18 Turn off steering override
    Prior to this commit, steering override was enabled by default. Since it is difficult to override the steering module by grabbing a moving steering wheel, and instead is much safer to use the E-stop or brake disabling methods to terminate OSCC control, the steering override system must instead be opted into. This commit adds a CMake option that enables users to include steering override detection if they choose to, and displays a warning as to why it is no longer enabled by default.
    [main.cpp]
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2017-11-17 Fix display initialization error
    Prior to this commit the display would not consistantly get initialized.
    The display's red led would be lit with a blank display.
    This commit moved the display initalization to happen before initializing the CAN buses.
    Tested by cycling power several times, running joysick commander, and verifying the display correctly reports when the system is enabled of disabled.
    [init.cpp]
2017-11-18 Fix failing gateway test
    [globals.h]
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2017-12-15 Fix for style guide
    [init.cpp]
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2018-01-12 Swapped high and low brake signal #defines, updated README.md to include Kia Niro
    [kia_niro.h]
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2018-01-15 Revert fault can protocol api header
    Prior to this commit the 'fault_can_protocol.h' file was changed to use the term
    global can but would make this branch a breaking change. This commit fixes that
    by reversing that change back to fault can protocol.
    [init.cpp]
2018-01-17 Remove API firmware dependency
    Prior to this commit the API was tightly coupled with the vehicle and firmware
    version which caused undesirable behavior when the two did not match. This
    commit fixes that by shipping the same desired state in the CAN messages
    regardless of vehicle and firmware versions.
    [brake_control.cpp]
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2018-01-18 Fix swapped voltages
    Prior to this commit the enable and disable calls in the firmware had inverse
    voltage pins DAC A and DAC B. This commit fixes that by reversing the voltage
    pins and confirming they do not cause a change in voltage after DAC A and DAC B
    read.
    [brake_control.cpp, throttle_control.cpp]
2018-01-19 Correct Naming
    Prior to this commit brake was copied into throttle and steering comments and
    the fault can protocol header was renamed to global. This commit fixes the wrong
    names.
    [init.cpp]
2018-01-23 Update numbers to be float values
    Prior to this commit some of the values that should be floats did not contain
    '.0' which could imply an integer. This commit fixes that by ensuring the float
    variables and constants have '.0' at the end if they happen to be whole numbers.
    [brake_control.cpp]
2018-01-23 Add Hysteresis for fault detection
    Prior to this commit moving the fault detection to use the same DAC reads as
    the operator override caused the fault detection to trip occationally due to
    noise in the signal. This commit adds hysteresis to determine if the DAC read
    is noise or a fault.
    [brake_control.cpp, kia_soul_ev.h, steering_control.cpp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]
2018-01-24 Move fault check to common libs
    Prior to this commit the function for checking for faults was duplicated in each
    module. This commit fixes that by moving the function into the common libs area.
    [brake_control.cpp, steering_control.cpp, throttle_control.cpp]
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2018-01-31 Keep header organization and add hysteresis
    Prior to this commit the kia niro header did not have the hysteresis parameter
    in the header file and the HIGH LOW variables were in the opposite order of the
    other vehicles. This commit fixes that by making the header file follow the
    format common among existing header files.
    [kia_niro.h]
2018-01-31 Move fault detection state into caller function
    The original implementation for checking for grounded signal inputs uses
    a function local static variable to store state between calls, which
    prevented the reuse of that logic for detecting other errors that have
    some time component. This commit extracts that state to a struct that
    caller functions can make static, so that the common fault checking
    logic can be reused for other cases.
    [steering_control.cpp, throttle_control.cpp]
2018-02-01 fault detection: distinguish between faults and fault conditions
    Some fault conditions have a time component where an error state has to
    be present for longer than an acceptable time period. In order to
    distinguish between these bad states and an actual fault detection this
    uses `condition` to indicate the anomalous state and `fault` to indicate
    a state that has been anomalous for longer than an acceptable period.
    [steering_control.cpp, throttle_control.cpp]
2018-02-02 operator override: Add time component to detection
    This commit adds a time factor for detecting operator overrides.
    Spurious noise induced by vehicle systems may cause the ADC ground
    reference to jitter which in turn can cause spurious overrides. This
    commit mitigates the noise induced overrides by requiring that the
    override condition is present for longer than the maximum transient
    noise duration.
    [brake_control.cpp, throttle_control.cpp]
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2018-04-04 Fix voltage spoof ranges
    Prior to this commit some of the voltage spoof ranges did not calculate to the
    correct value when multiplying and dividing by the STEPS_PER_VOLT against the
    the x_SPOOF_y_SIGNAL_VOLTAGE_z values. This commit fixes that by setting the
    x_SPOOF_y_SIGNAL_RANGE_z to something that calculates correctly.
    [kia_niro.h, kia_soul_ev.h]
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2018-04-30 Add arduino init to null implementation
    Prior to this commit the null implementation did not initialize the Arduino code
    in the firmware. This commit fixes that by adding arduino_init to the null
    firmware.
    [main.cpp]
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2018-09-25 Throttle operator override not being published
    Prior to thie commit the signal, "throttle_operator_override" in the message, "THROTTLE_REPORT(0x93)" did not report a status of driver's throttle override, whereas, the signal, "throttle_report_enabled" in the same message reports properly. The override report signals of steering/brake works well.
    The operator override was being generated but not published.
    Fix:
    Used operator override logic the brake is using.
    Verification:
    Ran `https://github.com/PolySync/oscc-check/blob/master/oscc-check.py` to enable all modules. Performed a throttle operator override.
    Verified throttle operator overide
    ```
    $ candump can0,093:7FF
    can0 093 [8] 05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
    [throttle_control.cpp]
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
